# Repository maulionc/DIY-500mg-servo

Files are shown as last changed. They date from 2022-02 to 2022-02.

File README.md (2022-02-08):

# DIY-500mg-servo
500mg servo for micro rc model







Electronic board

3 components :
1 atmel attiny1616 / 416 in  20-pin VQFN 3x3 mm
1 hall linear sensor : 49E-sot23 or A1304-sot23
1 cap 


To program Attiny1616 with one wire UDPI, you need to made UDPI programmer : (use arduino 3.3V)
https://create.arduino.cc/projecthub/john-bradnam/create-your-own-updi-programmer-1e55f1

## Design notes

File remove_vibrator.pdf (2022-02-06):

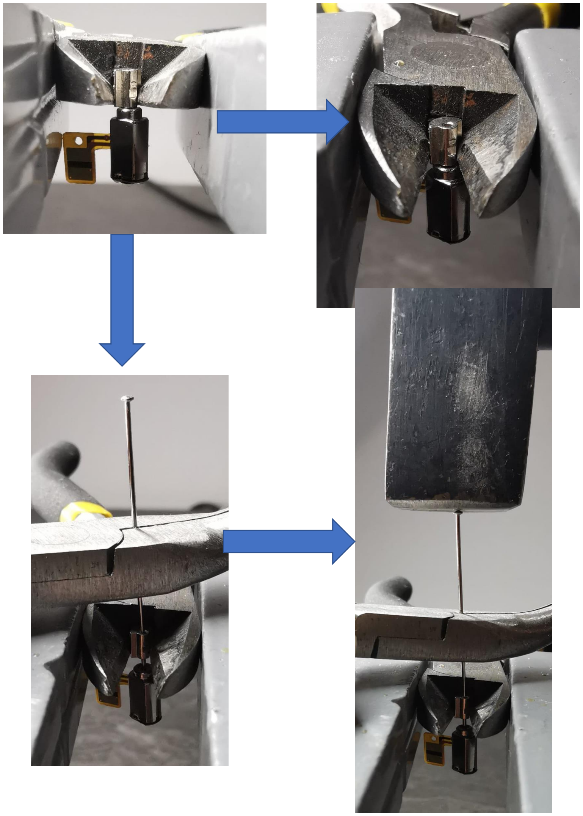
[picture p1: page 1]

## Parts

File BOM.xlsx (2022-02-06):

Bom DIY 500mg servo worm version
Mechanic
Function | Files name | Qty | material
axis |  | 2 | carbon diam 0,7mm
axis output |  | 1 | carbon diam 0,7mm
Mouting radial magnet | Support_magnet_V2 | 1 | Petg or resin
Principal parts | Support_moteur_3stages_vxxx | 1 | Petg or resin
top parts of the servos | renfort servo_3stages | 1 | Petg or resin
second gear | 24t_10t_m0.2_fin | 1 | Petg or resin
first gear | 24t_10t_m0.2 | 1 | Petg or resin
arm + next gear | 24t_m0.2_palonnier | 1 | Petg or resin
Worm gear | worm_gear_2.8mm_m0.2_0.65_1.5mm | 1 | Petg or resin
Electronics
name | Qty | Files name
attiny1616-mlf | 1
A1304-SOT23 hall sensor | 1
49E-sot23 | 1
Motor 4*3*6,5mm | 1
magnet radial 2*1mm | 1
PCB flex from OSH park | 1 | board1616_1servo_small.brd (https://github.com/maulionc/DIY-500mg-servo/blob/main/Electronic/board1616_1servo_small.brd)

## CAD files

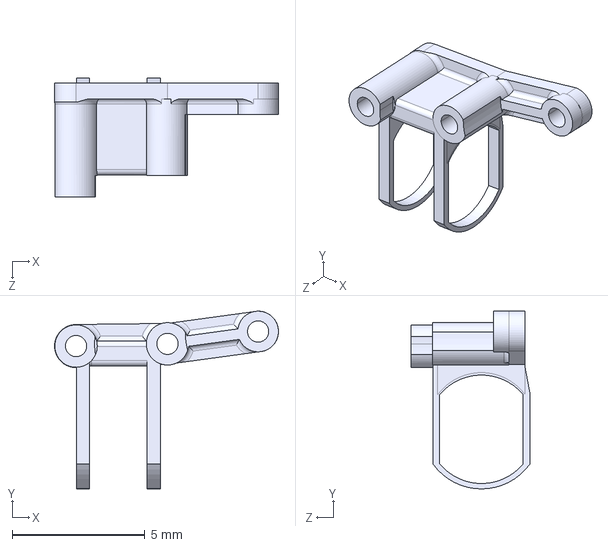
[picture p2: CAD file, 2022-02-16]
Step files/Support_moteur_3stages_v5.STEP
8.45 x 6.71 x 4.48 mm

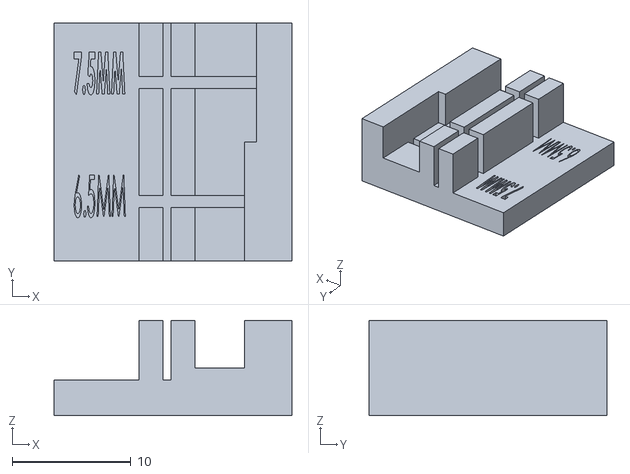
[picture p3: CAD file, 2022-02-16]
STL files/Tool_axis.STL
20.0 x 20.0 x 8.00

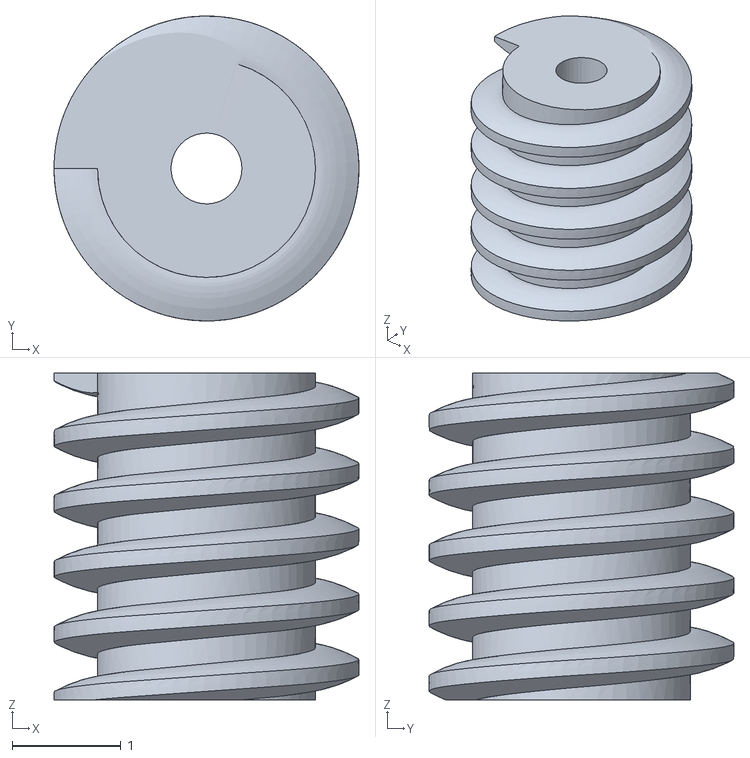
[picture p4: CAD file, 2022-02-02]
STL files/worm_gear_2.8mm_m0.2_0.65.STL
2.80 x 2.80 x 3.00

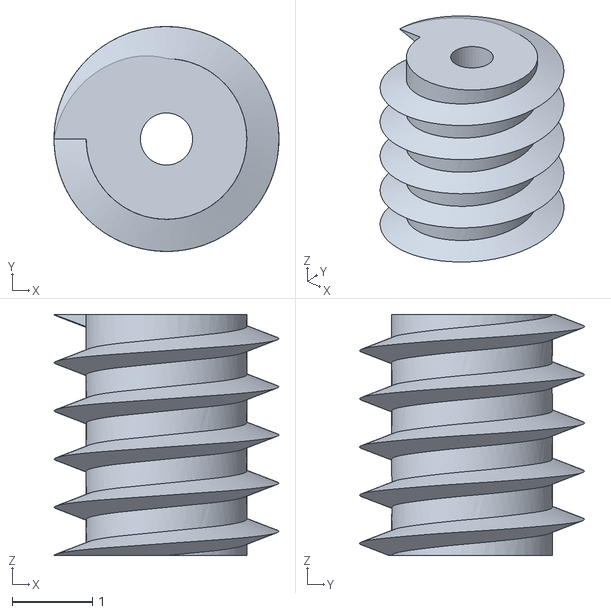
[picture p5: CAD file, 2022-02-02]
STL files/worm_gear_2.8mm_m0.2v2_0.65.STL
2.80 x 2.80 x 3.00

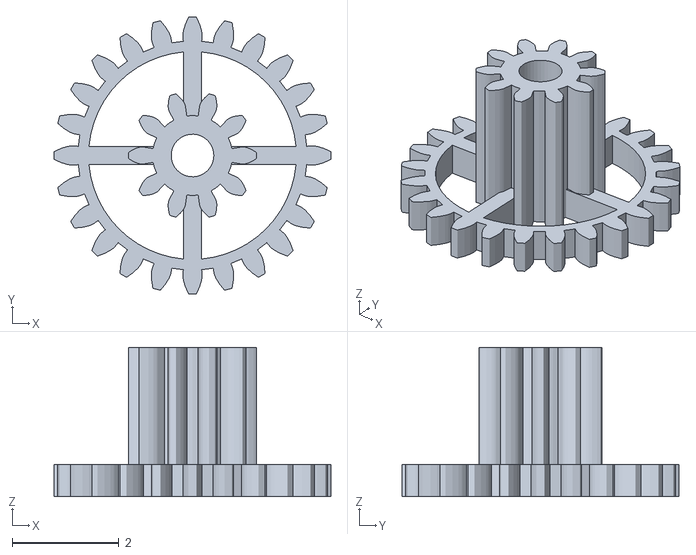
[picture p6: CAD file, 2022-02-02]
STL files/24t_10t_m0.2.STL
5.20 x 5.20 x 2.80

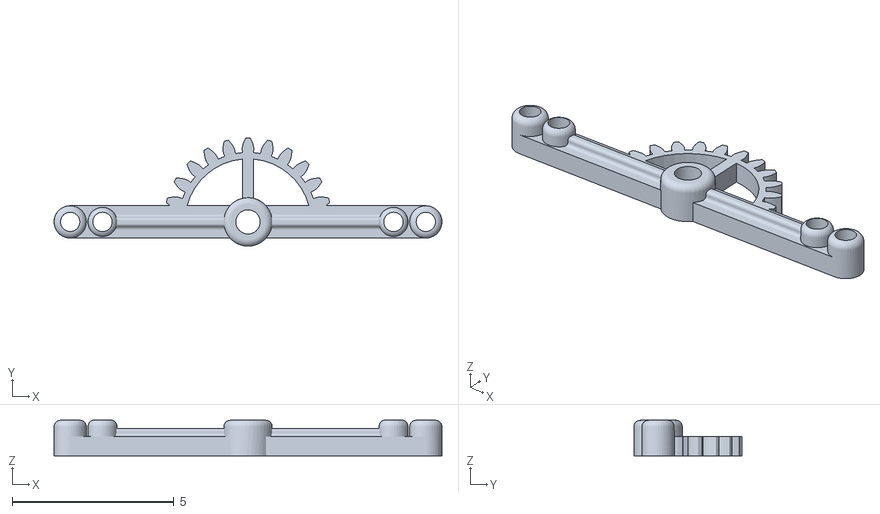
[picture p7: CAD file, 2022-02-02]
STL files/24t_m0.2_palonnier_v2.STL
12.0 x 3.35 x 1.10

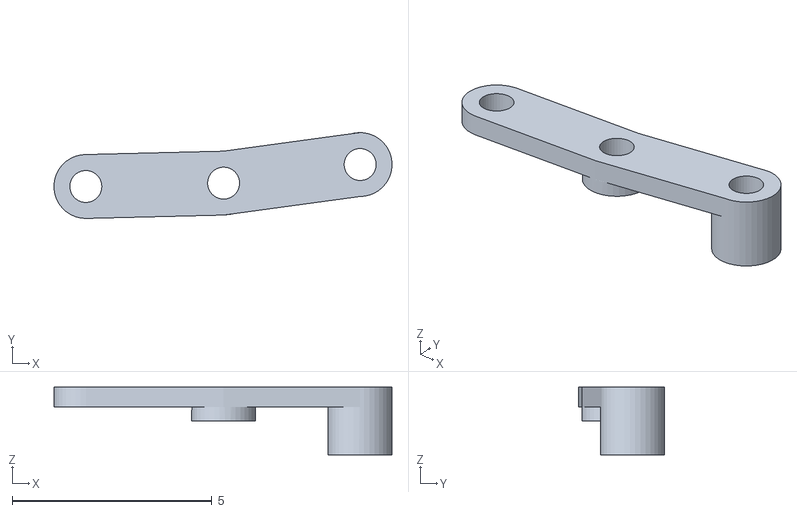
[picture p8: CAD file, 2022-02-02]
STL files/renfort servo_3stages.STL
8.46 x 2.15 x 1.70

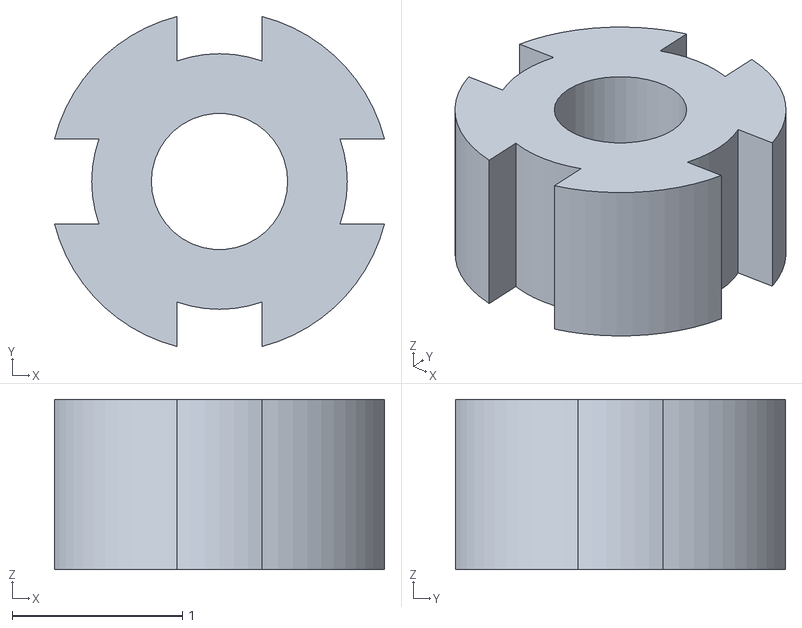
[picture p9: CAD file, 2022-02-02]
STL files/Support_magnet_V2.STL
1.94 x 1.94 x 1.00

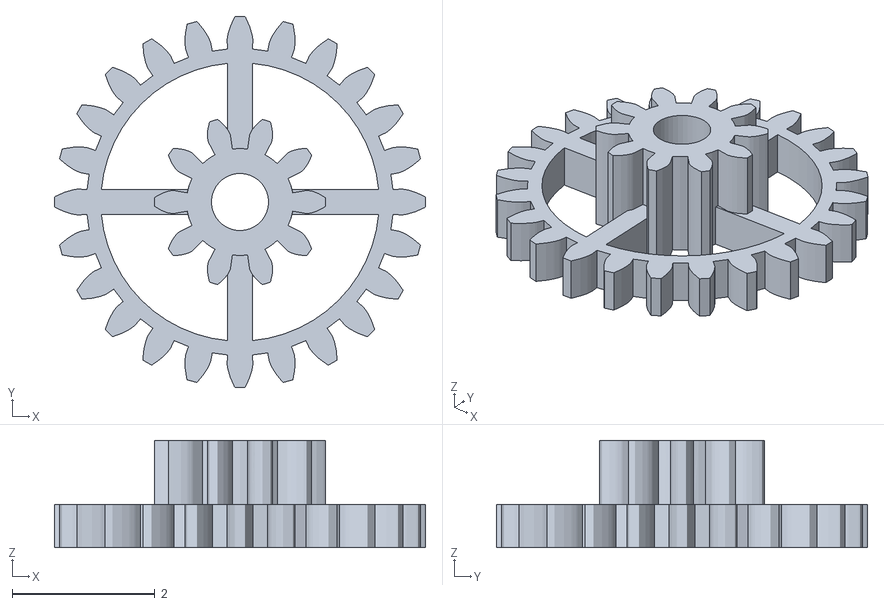
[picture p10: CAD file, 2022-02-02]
STL files/24t_10t_m0.2_fin.STL
5.20 x 5.20 x 1.50

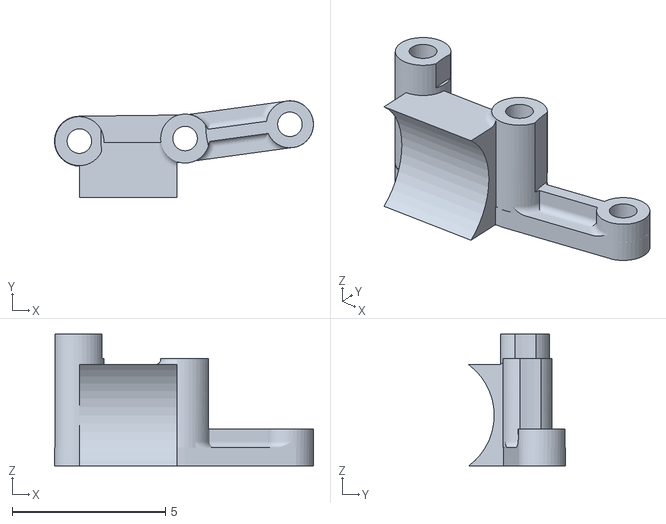
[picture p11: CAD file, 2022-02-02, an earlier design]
STL files/Support_moteur_3stages_v3.STL
8.45 x 3.15 x 4.30

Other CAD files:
STL files/Support_moteur_3stages_v5.STL

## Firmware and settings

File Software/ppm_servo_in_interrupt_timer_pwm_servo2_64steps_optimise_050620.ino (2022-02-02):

/*Servo Driver for Attiny1616
 * Maulion Charles 02/01/2020
 * Use Megatinycore library
 * Internal clock 10mhz
 * !!!!!!!!!!use millis TCB0!!!!!!!!!!!!! 
 * 
 * PA4 : hall effect
 * PA2 : servo signal
 * 
 * For now 2 outputs : 
 * PB4/PB5 = -motor
 * PC1/PC2 = +motor
 * 
 * for the pcb 
 * PB2/PB3/PB4/PB5 = -motor
 * PB0/PC0/PC1/PC2 = +motor
 * 
 * adjust Steps => adjust output frequency => 64 steps arround 2khz
 * 
 * 
 * 
 */
 
// Install Pin change interrupt for a pin, can be called multiple times

int pciTime = 0;
byte prev_pinState = 0;
unsigned long pwmPeriod = 0 ;
int pwmTimer = 0;

int PW = 1500;
byte  pwmFlag = 0 ;


/*Pwm count*/
volatile unsigned char _time_count=0;      // time++
int steps = 8; // lower steps control but higher frequency output motor 8,16,32,64,128


int PWM1=0;
int PWM2=0;
int duration =0;
int setpoint =0;


int srv_min_read=1000;//850
int srv_max_read=2000;
int srv_mid_val=1500;
int delta = 150;
int angle_out_min=512-delta;//450
int angle_out_max=512+delta;//450
int srv_value=1500;




/*byte debug*/
byte debug = 0;


/**********servo**********/
int ADC_SetPoint_S1 = 0;
int ADC_SetPoint_S1_in = 0;
int ADC_SetPointOld_S1 = 0;
int ADC_ServoPoti_S1 = 512;
int ADC_ServoPotiOld_S1 = 512;
int dutyCycle_S1 = 10; // 10 - 255
int ADCdiff_S1 = 0;
int timeDiff_S1 = 0;





//Change values below to adapt your motor
//Set MAX_DUTYCYCLE_S1 and MAX_DUTYCYCLE_S2 to 75 for the first test run!

#define P_FRACTION_S1 4          //0.0 - 10.0 (0.3)JJKWAng use =1
#define I_FRACTION_S1 4          //0.0 - 10.0 (0.3)JJKWAng use =1
#define D_FRACTION_S1 4          //0.0 - 10.0 (4.0)JJKWAng use =1
#define V_WINDOW_S1 4             //10 - 1000 (25)
#define MIN_DUTYCYCLE_S1 steps/2     //0 - 255 (125)
#define MAX_DUTYCYCLE_S1 steps     //0 - 255 (255)
#define SOFT_START_S1 1.00          //0.00 - 1.00 (0.30) 1.00 = OFF
#define EMERGENCY_SHUTDOWN_S1 0  //0 - 1000 (300), 0 - OFF, Stops motor if blocked



#define SERVO_SENSOR_S1 0       //Analog input servo sensor A4



/* Pin interrupt servo, read servo pulse Input*/
ISR (PORTA_PORT_vect) // handle pin change interrupt for A2
{
PORTA.INTFLAGS=4; //we know only PB0 has an interrupt, so that's the only flag that could be set. Px0=1 / Px2=4 etc

pciTime = micros();  
    if(prev_pinState == 0 )
        {          // and the pin state has changed from LOW to HIGH (start of pulse)
        prev_pinState = 1;                                     // record pin state
        pwmPeriod = pciTime - pwmTimer;                     // calculate the time period, micro sec, between the current and previous pulse
        pwmTimer = pciTime;                                    // record the start time of the current pulse
        }
      else if (prev_pinState == 1 )
        { // or the pin state has changed from HIGH to LOW (end of pulse)
        prev_pinState = 0;                                     // record pin state
        PW = pciTime - pwmTimer;                            // calculate the duration of the current pulse
        pwmFlag = HIGH;   // flag that new data is available
      //  if(i+1 == RC_inputs) RC_data_rdy = HIGH;
        }



}  



/*Interrupt PWM*/
ISR(TCB1_INT_vect)
{
  /*
  static uint8_t t;
  if ( t < PWM1 ) PORTB.OUTSET = _BV(4) | _BV(5);
  else            PORTB.OUTCLR = _BV(4) | _BV(5);
  if ( t < PWM2 ) PORTC.OUTSET = _BV(1) | _BV(2);
  else            PORTC.OUTCLR = _BV(1) | _BV(2);
  t += 4;     // 64 steps
  TCB1.INTFLAGS = TCB_CAPT_bm;
  */

  
  if(_time_count<steps)
  {
    
//TCB1.INTFLAGS= TCB_CAPT_bm; //clear interrupt flag


if ( _time_count < PWM1 ) PORTB.OUTSET = _BV(2) |_BV(3) |_BV(4) | _BV(5);
else            PORTB.OUTCLR = _BV(2) |_BV(3) |_BV(4) | _BV(5);
if ( _time_count < PWM2 ) 
{
  PORTC.OUTSET = _BV(0) |_BV(1) | _BV(2);
  PORTB.OUTSET = _BV(0);
}
else            
{
  PORTC.OUTCLR = _BV(0) |_BV(1) | _BV(2);
  PORTB.OUTCLR = _BV(0);
}
_time_count++;           // 변수 증가  0~255 > 0~255 반복
  }
  

  else 
  {
    _time_count=0;

  }
TCB1.INTFLAGS= TCB_CAPT_bm; //clear interrupt flag

}


 
 

 
void setup() {  
PORTB.DIR = 0b00111101;  // set PORTB PB0/PB2/PB3/PB4/PB5
//PORTB.DIR = 0b00110000;  // set PORTB PB4/PB5
PORTC.DIR = 0b00000111; // set PORTB PC0/PC1/PC2
//PORTC.DIR = 0b00000110; // set PORTB PC1/PC2
PORTA.DIR = 0b00000000; //PA2 in servo / PA4 in feedback

/*input Servo pin  interrupt*/
PORTA.PIN2CTRL=0b00001001; //PULLUPEN=1, ISC=1 trigger both


if (debug == 1)
{
Serial.begin(115200);
delay(10);
Serial.println("Startup");
}


/*configure timer TCB1 for pwm */

TCB1.CTRLA= TCB_ENABLE_bm;
TCB1.CNT=0;
TCB1.CTRLB=0; // periodic interrupt mode
TCB1.CCMP = 78*2; // 
TCB1.INTCTRL=TCB_CAPT_bm;
//TCB1.CTRLA= TCB_CLKSEL_CLKDIV2_gc | TCB_ENABLE_bm;

delay(2000);

}

void servo1()
{
  //Servo 1 ----------------------------------------------------------
  ADC_ServoPoti_S1 = analogRead(SERVO_SENSOR_S1);     // reads the servo sensor (between 0 and 1023) 

  ADCdiff_S1 = srv_value - ADC_ServoPoti_S1  ;
  
  dutyCycle_S1 = abs(ADCdiff_S1) * P_FRACTION_S1;
  dutyCycle_S1 += timeDiff_S1 * I_FRACTION_S1;
  dutyCycle_S1 += abs(ADC_SetPointOld_S1 - ADC_SetPoint_S1) * D_FRACTION_S1;
    
  if(SOFT_START_S1 * timeDiff_S1 < 1){
    dutyCycle_S1 = dutyCycle_S1 * (SOFT_START_S1 * timeDiff_S1);
  }
  
  timeDiff_S1++;
  
  if(dutyCycle_S1 < MIN_DUTYCYCLE_S1 && dutyCycle_S1 > 0){
    dutyCycle_S1 = MIN_DUTYCYCLE_S1;
  }
  
  if(dutyCycle_S1 > MAX_DUTYCYCLE_S1){
    dutyCycle_S1 = MAX_DUTYCYCLE_S1;
  }
  
  if(dutyCycle_S1 < 0){
    dutyCycle_S1 = 0;
  }
  
  
  if(abs(ADCdiff_S1) < V_WINDOW_S1){
    dutyCycle_S1 = 0;
    timeDiff_S1 = 0;
  }

  if(dutyCycle_S1 == MAX_DUTYCYCLE_S1 && timeDiff_S1 > EMERGENCY_SHUTDOWN_S1 && EMERGENCY_SHUTDOWN_S1 > 0){
  PWM1 = 0;
  PWM2 = 0;
    //delay(1000);
    timeDiff_S1 = 0;
  }
  else{  
    if(ADCdiff_S1 > 0){
      PWM1=0;
      PWM2 = dutyCycle_S1;
    }
    if(ADCdiff_S1 < 0){
      PWM1 = dutyCycle_S1;
      PWM2 = 0;
    }
  }
  

  ADC_SetPointOld_S1 = ADC_SetPoint_S1;
  ADC_ServoPotiOld_S1 = srv_value;


  
}
 
 
void loop() {
/*
if (PW < srv_min_read) // a check
{
  PW = srv_min_read;
}
if (PW > srv_max_read)
{
  PW = srv_max_read;
}
*/

//srv_value = map(PW,850,2000,300,550);// no logic but thats run, need to be check
srv_value = map(PW,srv_min_read,srv_max_read,angle_out_min,angle_out_max);// no logic but thats run, need to be check

 if ( debug == 0)
 {
delay(1);
 }
 

 servo1();

 if ( debug == 1)
 {
   Serial.print(PW);  Serial.print("\t"); Serial.print(_time_count);  Serial.print("\t"); Serial.print(srv_value); Serial.print("\t");  Serial.print(ADC_ServoPoti_S1);

 }



}

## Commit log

2022-02-02 Create STL files
2022-02-16 Add files via upload
    tool to cut 0.7mm carbon axis at the good lenght
    [Tool_axis.STL]
2022-02-16 Add files via upload
    motor rings are added
    [Support_moteur_3stages_v5.STL]
